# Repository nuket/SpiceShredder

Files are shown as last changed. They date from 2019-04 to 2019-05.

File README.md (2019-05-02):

# IKEA Spice Shredder

This is a project to motorize an [IKEA IHÄRDIG](https://www.ikea.com/ms/en_US/usearch/?query=IH%C3%84RDIG) spice grinder using a 3D-printed drill adapter.

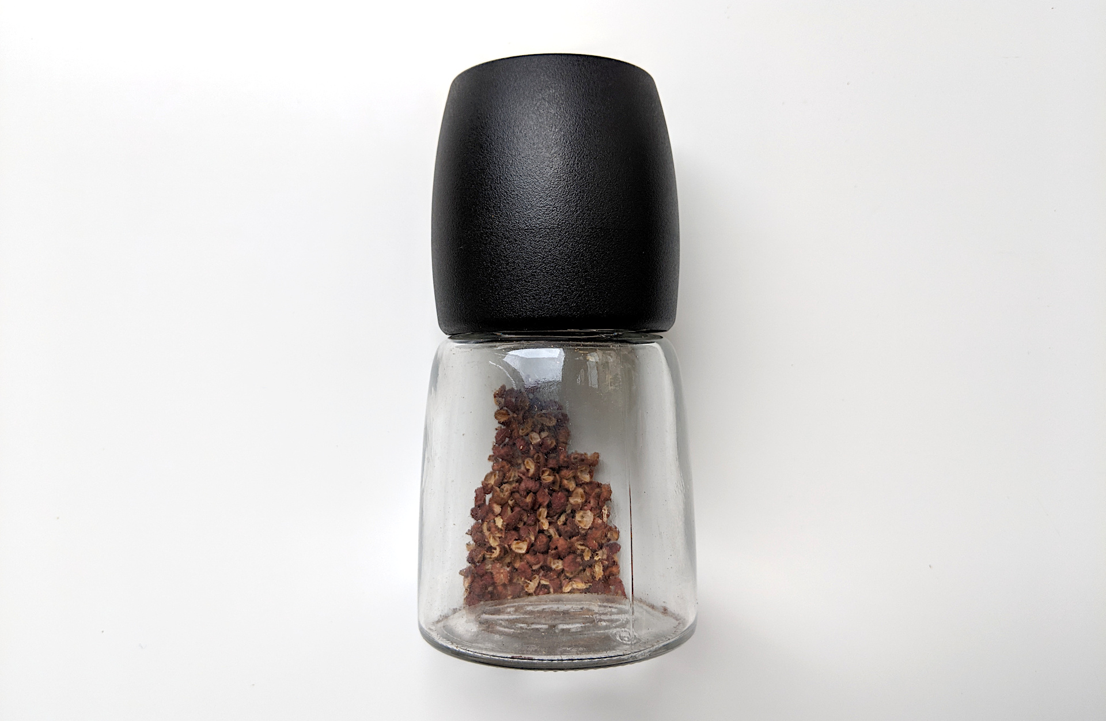
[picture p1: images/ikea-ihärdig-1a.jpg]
IKEA IHÄRDIG spice grinder


Anytime you motorize a grinder, it should be called a shredder.

## Video

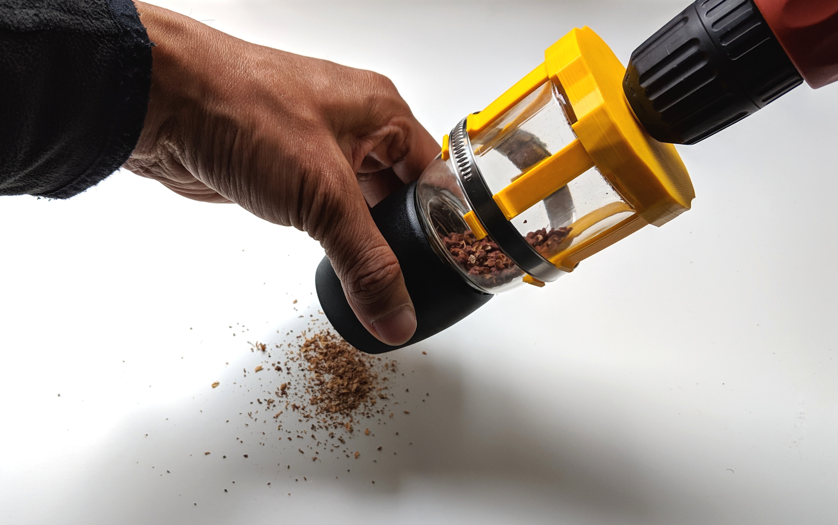
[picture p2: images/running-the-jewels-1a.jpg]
Click to open video of Spice Shredder in action (https://vilimpoc.org/media/running-the-spiceshredder-1920p24-4096k.mp4)


Click to open video of the Spice Shredder in action.

## Rationale

After spending 15 minutes using this spice grinder to make curry powder from whole spices by hand (and nearly getting a repetitive stress injury with the clockwise twisting), I decided that the best solution would be to hook up a drill, and use electricity to do the work instead.

Electric coffee and spice grinders are expensive. IKEA is affordable. And 3D printing is pretty cheap too, once you have a printer.

So the idea is to create an adapter that can grip the spice grinder and rotate it rapidly.

It took three modeling attempts to do so, and since you learn a lot from failure, the whole process is captured here.

## Measurements

The IHÄRDIG spice grinder has a 6.5cm diameter base, and tapers slightly inwards about 1 - 1.5mm at  5 centimeters up the cylinder. I don't have a measurement [caliper](https://en.wikipedia.org/wiki/Calipers), so I had to eyeball these dimensions.

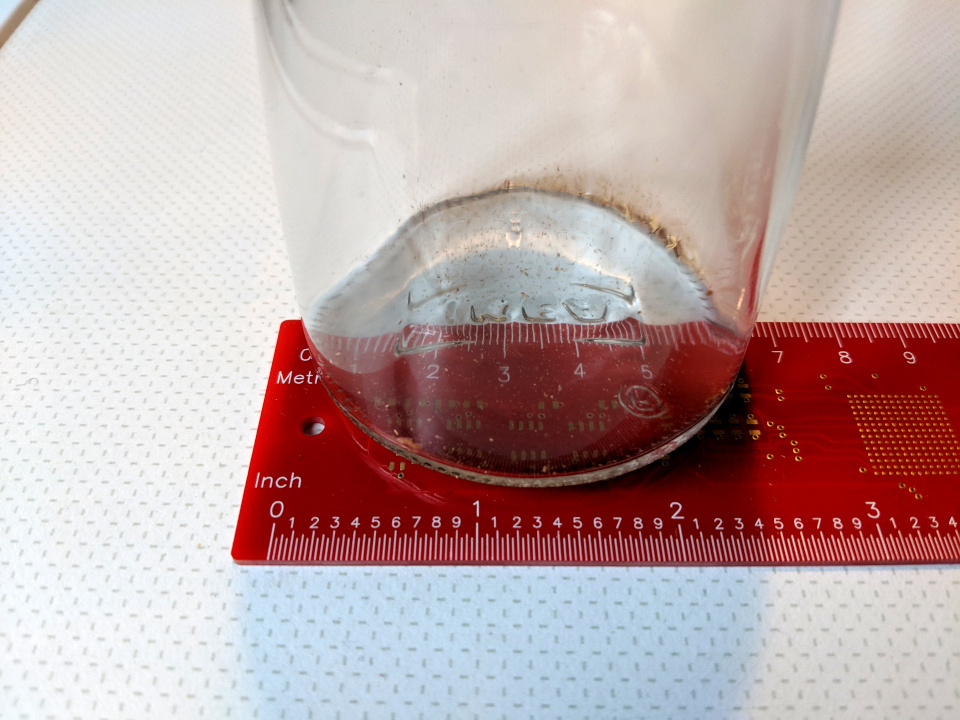
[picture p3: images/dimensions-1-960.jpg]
Spice grinder measurements


The business end of the largest hex-head driver in a standard IKEA [FIXA](https://www.ikea.com/ms/en_US/usearch/?query=fixa) toolkit is around 3 - 3.5mm per edge and 1cm long.

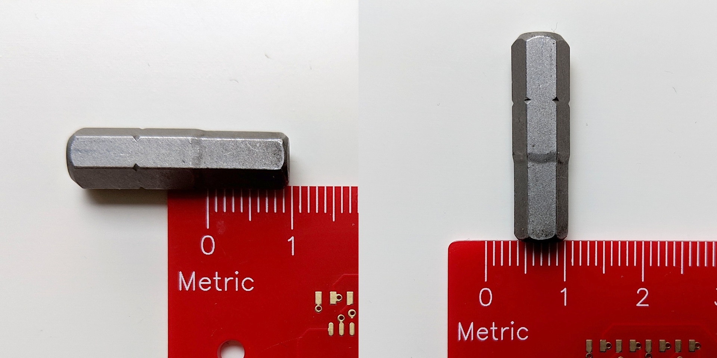
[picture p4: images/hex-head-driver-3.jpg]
IKEA FIXA hex-head driver measurements


## Model 1 (Fail)

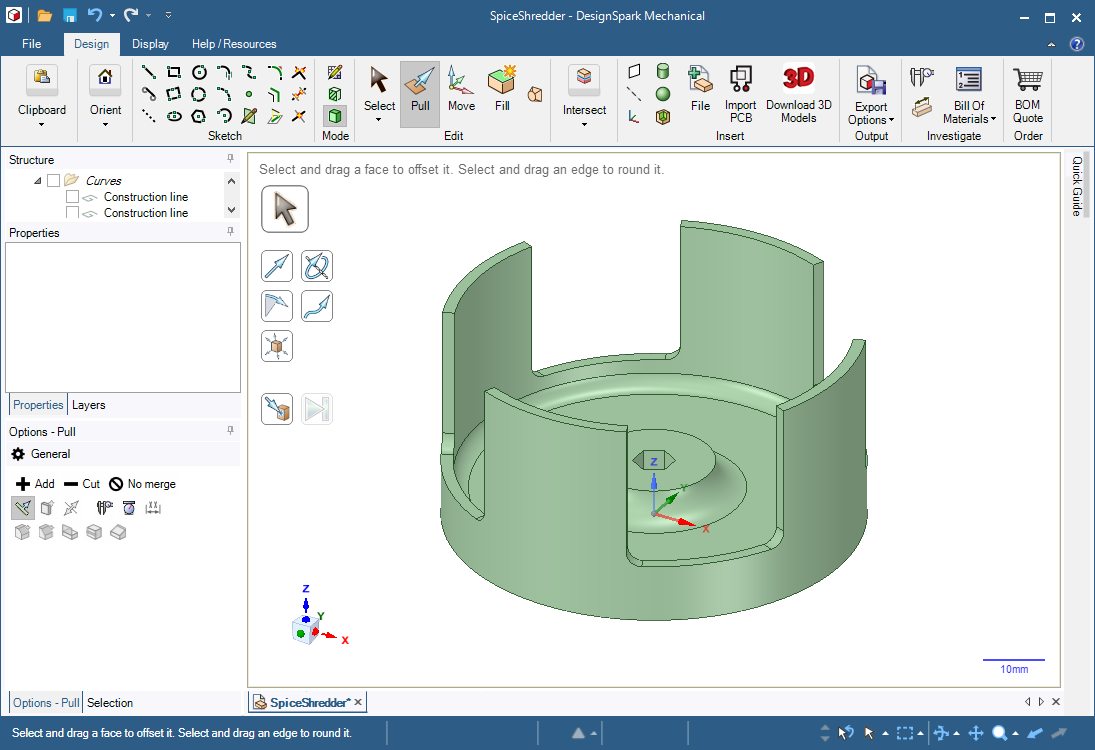
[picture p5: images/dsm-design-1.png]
Model 1 Design in DesignSpark Mechanical


This does not work because the way the walls are printed up, they are brittle and inflexible.

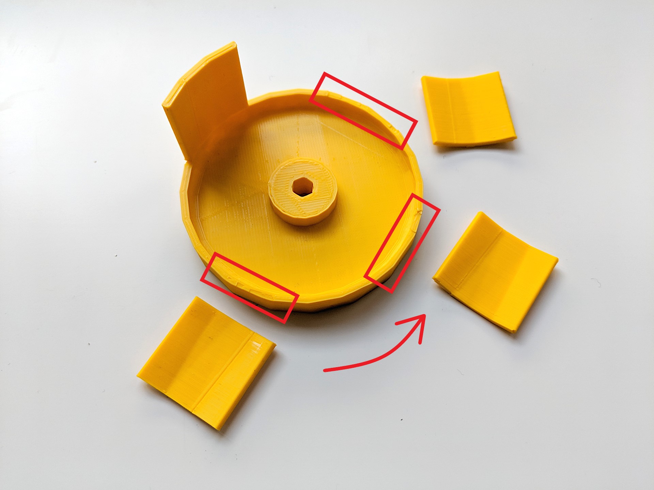
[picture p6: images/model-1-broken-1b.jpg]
Broken tines after printing


The base is printed in concentric circles in the direction of the arrow. The 2mm-thick tines are attached in the same way. They simply _cannot_ flex, so at every connection point to the base, these parts break off instantly.

Also, the hole for the hex-head driver is too small.

## Model 2 (Fail)

This model splits the adapter into two pieces that are assembled: the base and the tines.

This is necessary, because there is no way to mix the direction of printing within a single model — the base and tines use fibers perpendicular to one another.

The base can be printed cleanly from bottom to top with concentric circles and infill, and it can be completely rigid.

The [tines](https://www.dictionary.com/browse/tines) must be printed lengthwise, because we need long polymer fibers that are flexible, unlike the densely-stacked short fibers in Model 1.

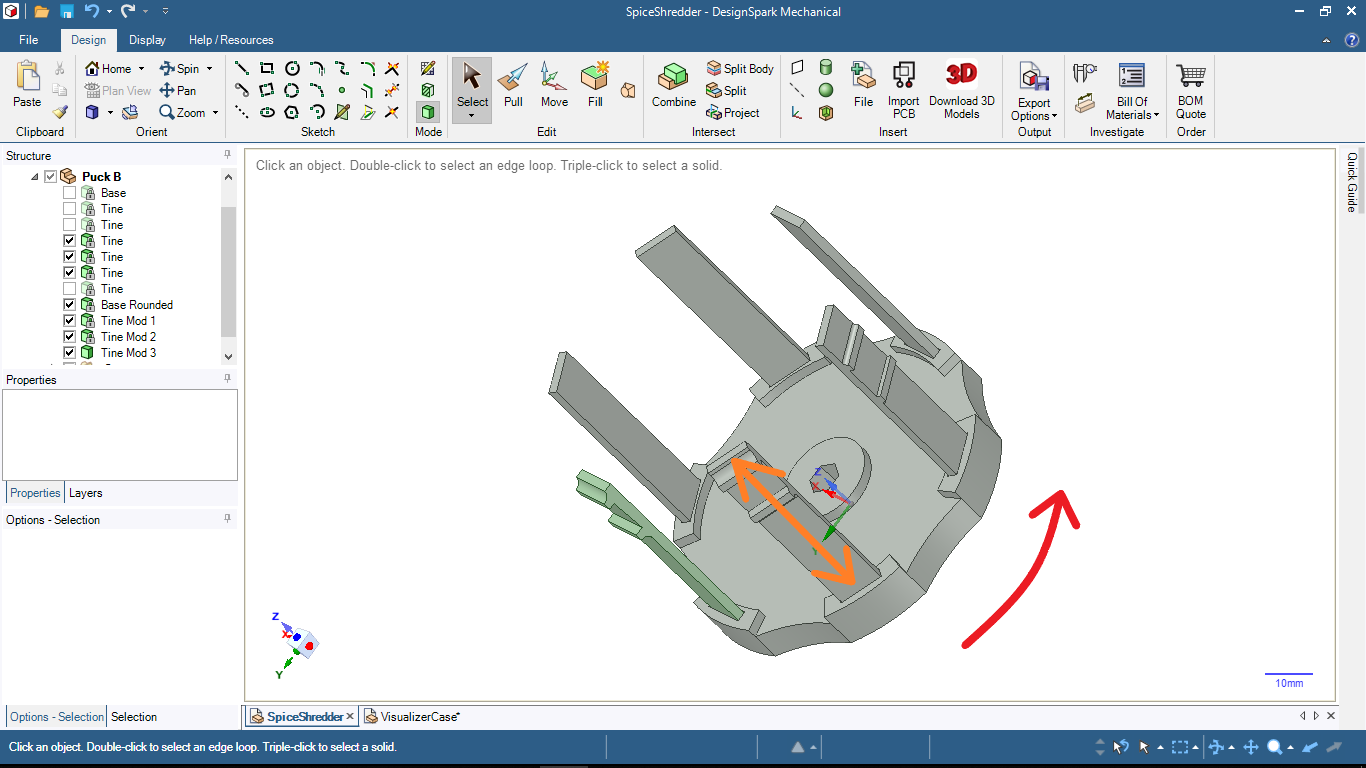
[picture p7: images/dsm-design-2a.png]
Model 2 Design in DesignSpark Mechanical


The picture above shows three slightly different designs for the tines, to be tested out.

This model almost works, the hole for the hex-head driver is perfectly sized. The problem is that the cylinder which grips the hex-head driver is slightly too short. So the driver sticks out by about 0.5mm, and it runs into the bottom of the spice grinder.

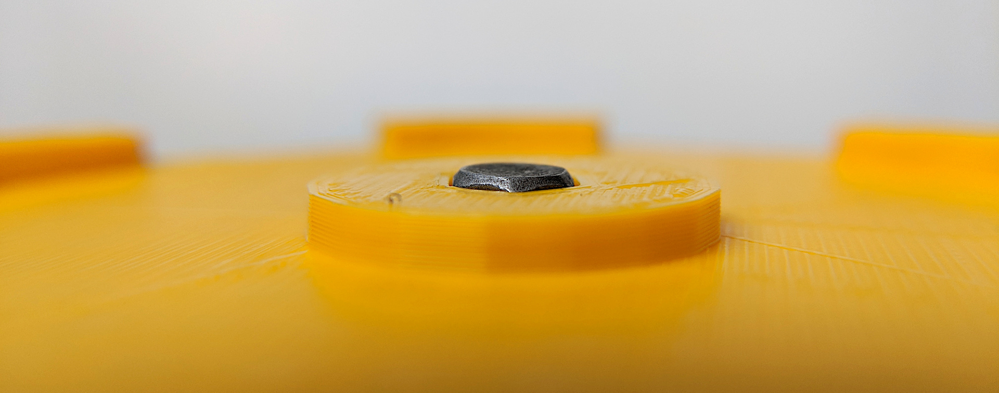
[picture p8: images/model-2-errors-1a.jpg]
Hex-head driver sticks out of cylinder


Also, there's some wasted plastic here.

## Model 3 (Win!)

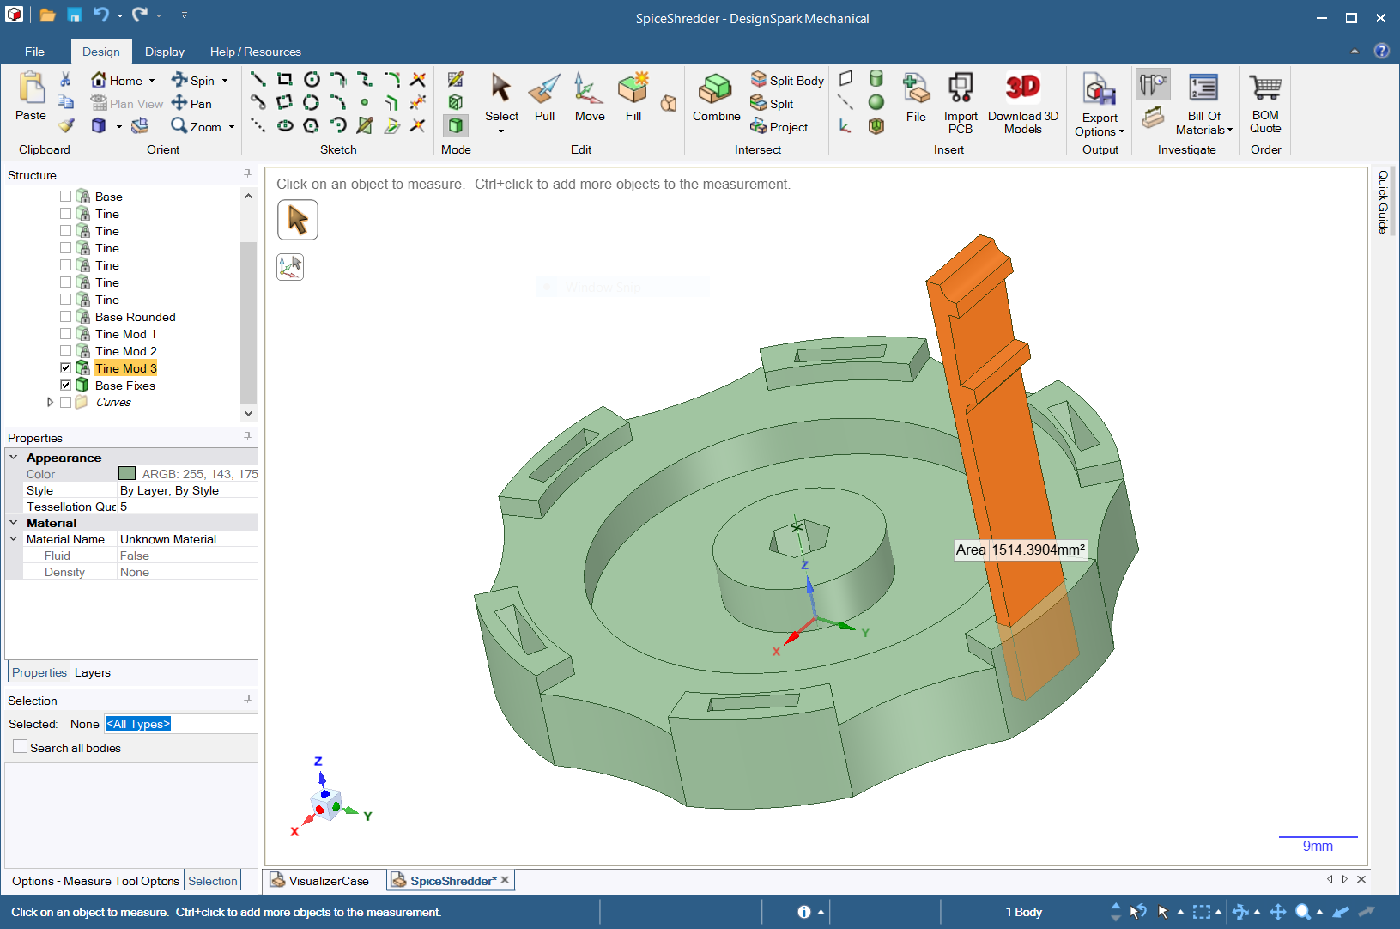
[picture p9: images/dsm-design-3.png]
Model 3 Design in DesignSpark Mechanical


This model corrects all of the issues in the other designs, and removes some unused plastic.

After printing a single test copy of the most-likely best tine model, I went ahead and printed five more like it. Then, I assembled these items together.

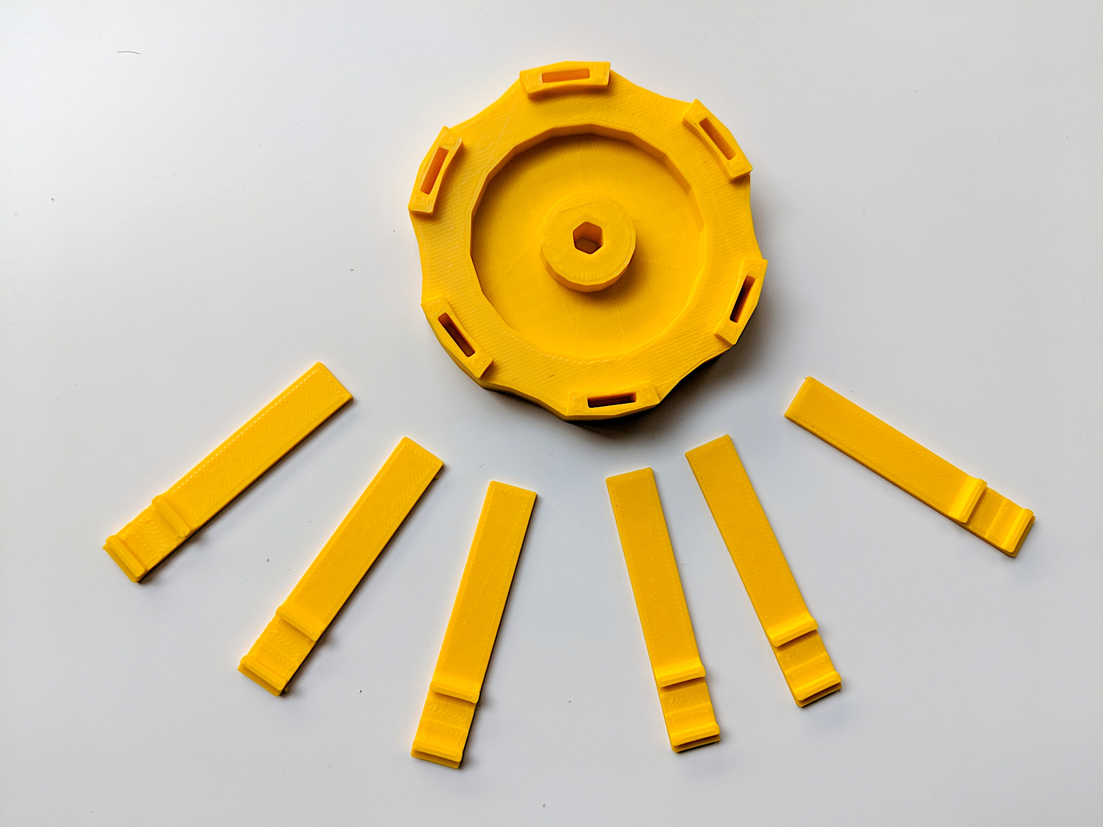
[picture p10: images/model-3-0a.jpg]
Printed Model 3 with base and tines separated


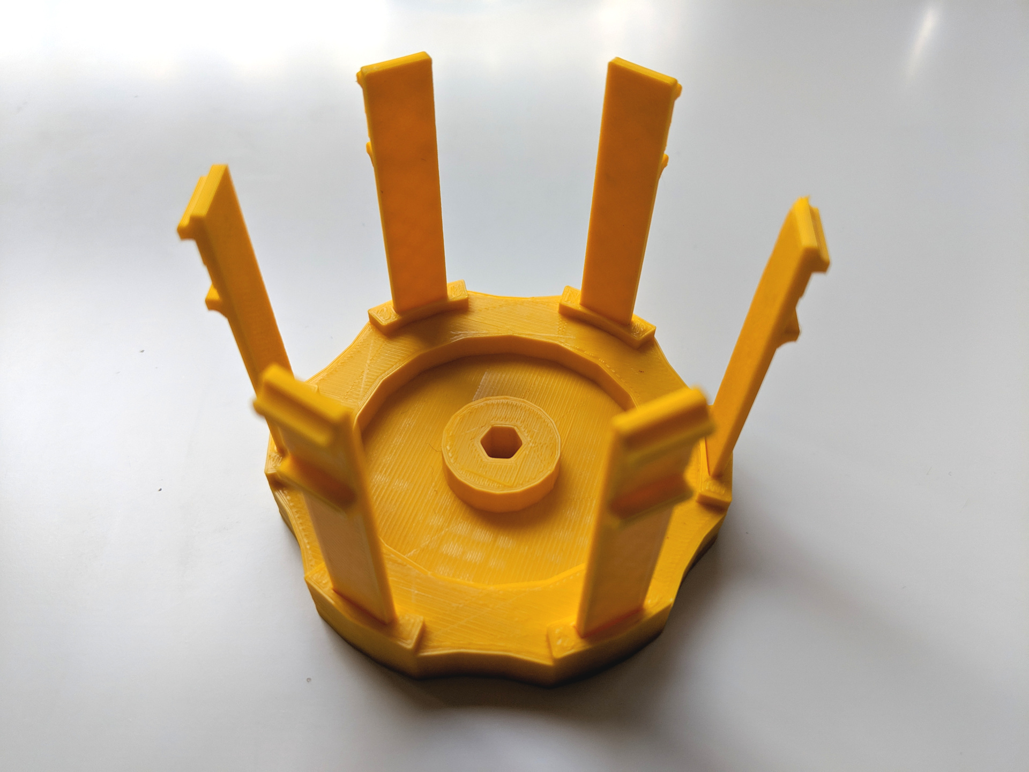
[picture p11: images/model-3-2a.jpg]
Printed Model 3 with tines slotted into the base


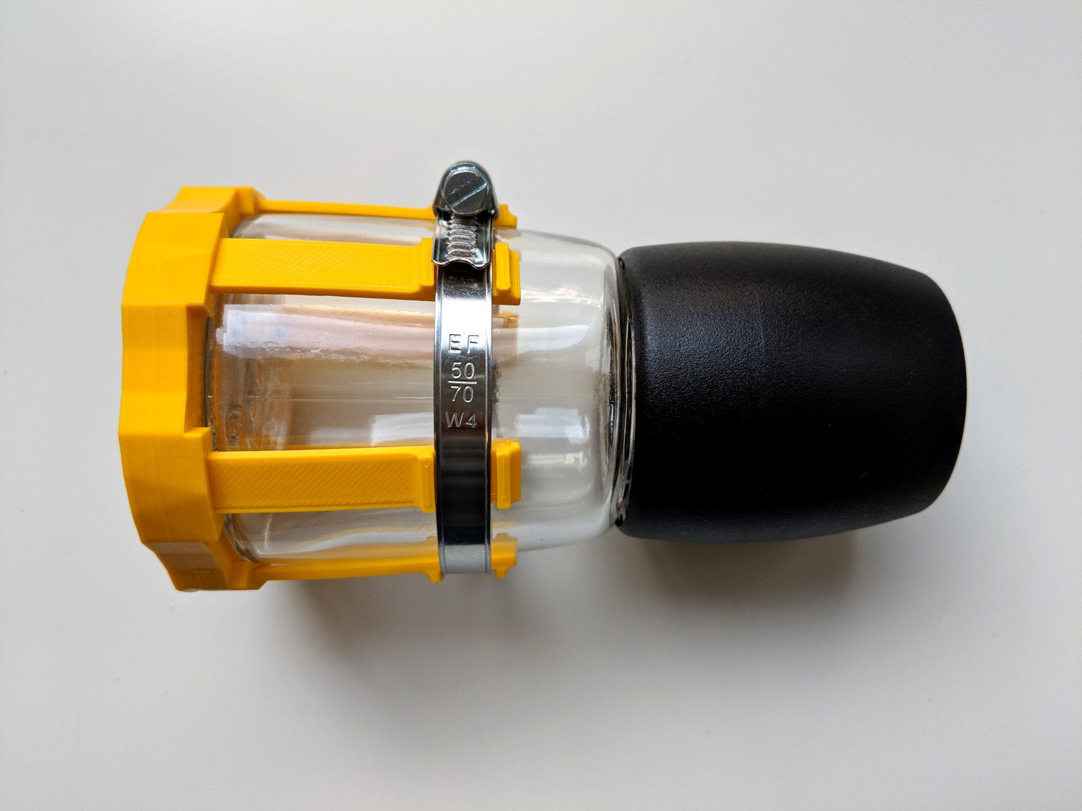
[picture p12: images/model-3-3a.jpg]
Printed Model 3 attached to IHÄRDIG spice grinder with hose clamp


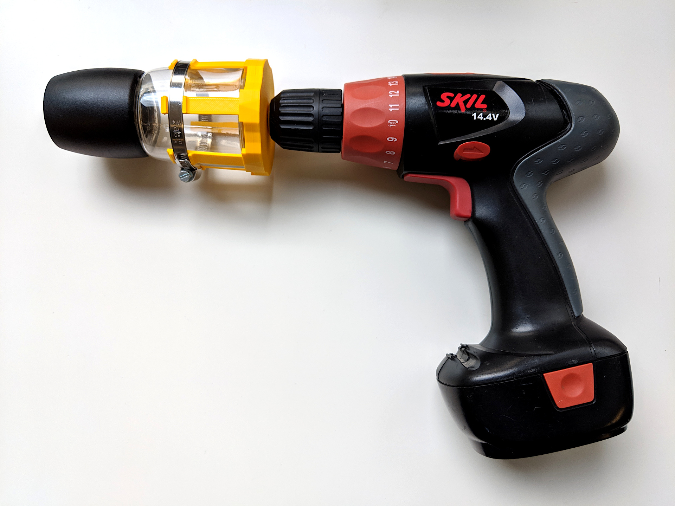
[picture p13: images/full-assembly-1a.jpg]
Full assembly attached to cordless power drill


To make the adapter grip the glass, we tighten an adjustable hose clamp around the tines, pressing them against the glass jar.

There's one other feature to this tine as well. Because the top of the glass jar is narrower than the base, we have to add a small inclined plane, to account for when the hose clamp grips all 6 tines and they all flex inward to grip the glass.

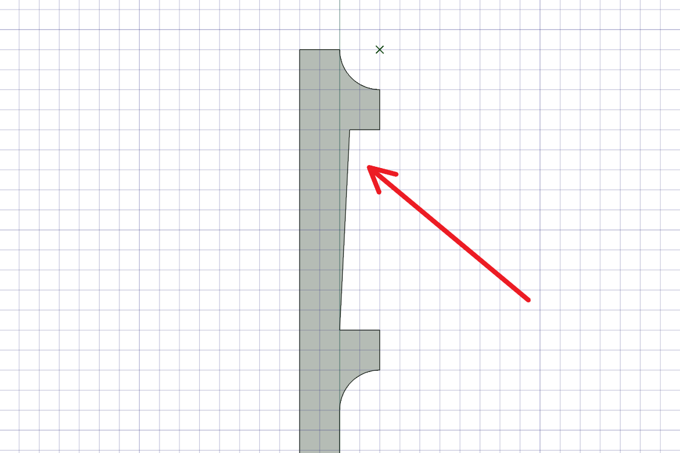
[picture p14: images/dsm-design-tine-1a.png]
Illustration of tine with inclined plane indicated


The hose clamp is standard stainless 9mm width x 50 - 70mm diameter. In Germany, these are easy to source online; in the US, I'm pretty sure any Home Depot would have them.

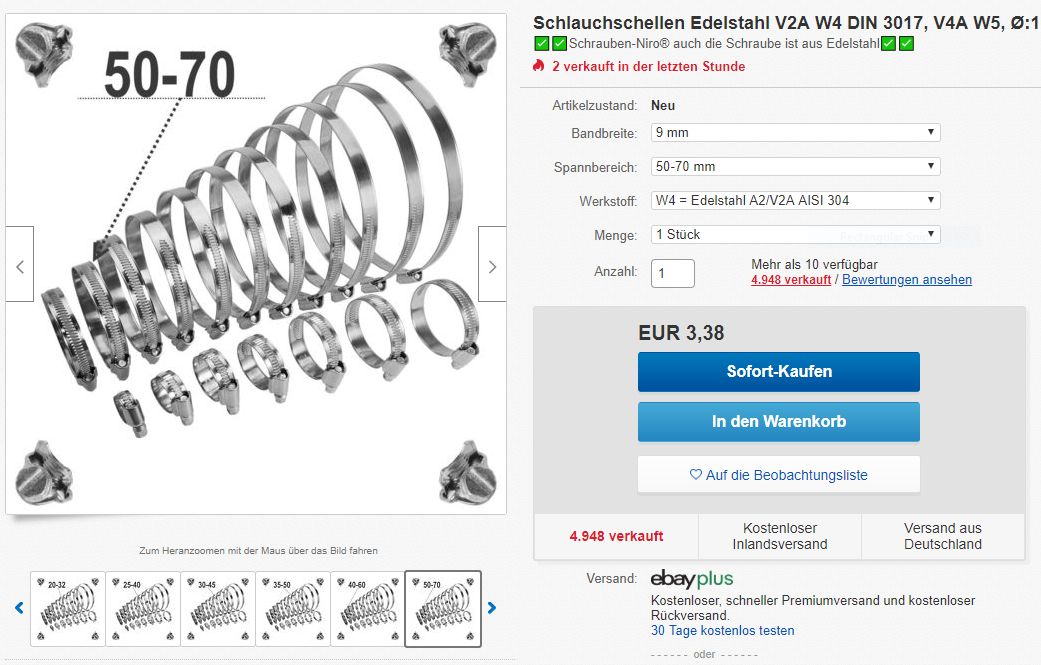
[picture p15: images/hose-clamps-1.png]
Picture of hose clamp auction on eBay Germany


Happy grinding, people! 😉

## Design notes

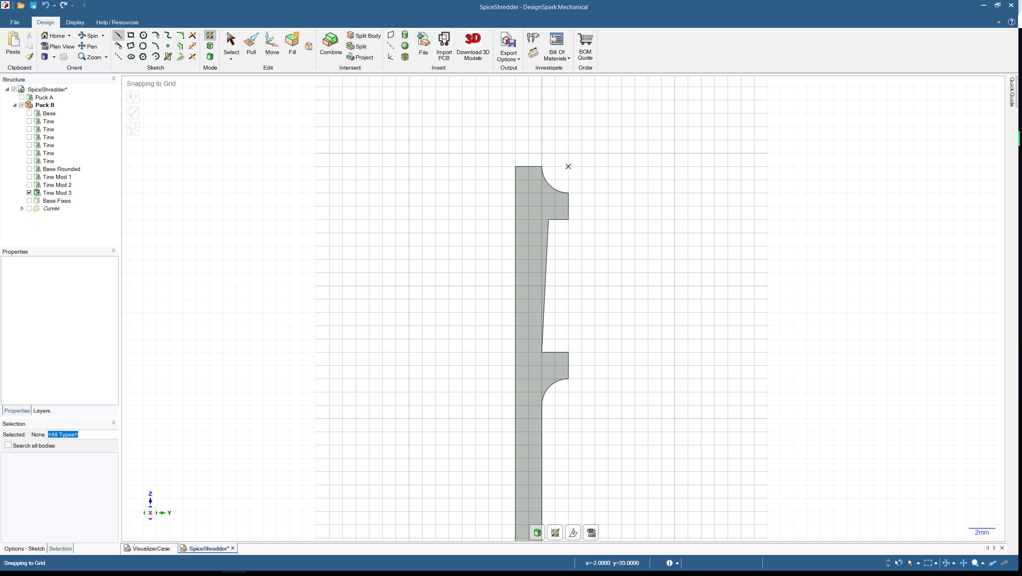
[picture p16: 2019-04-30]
images/dsm-design-tine-1.png

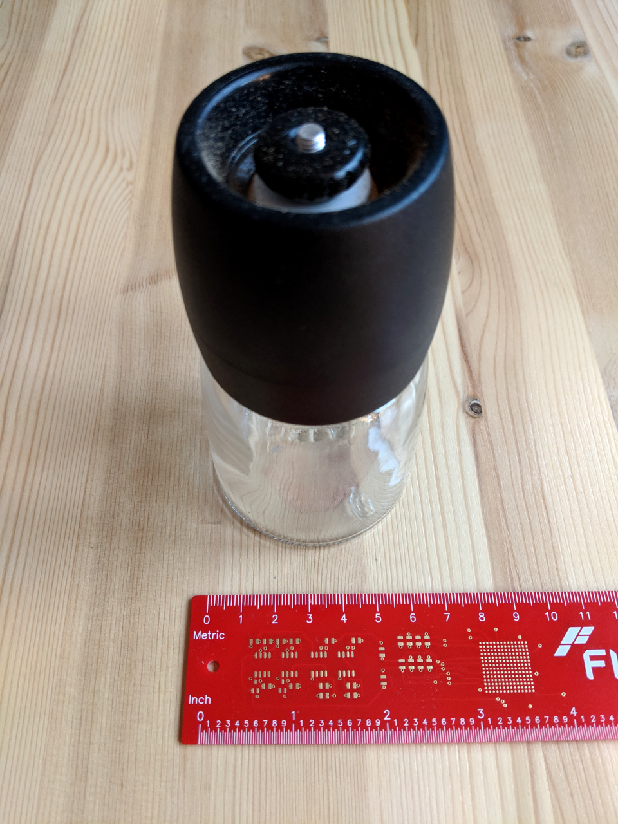
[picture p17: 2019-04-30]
images/dimensions-2-960.jpg

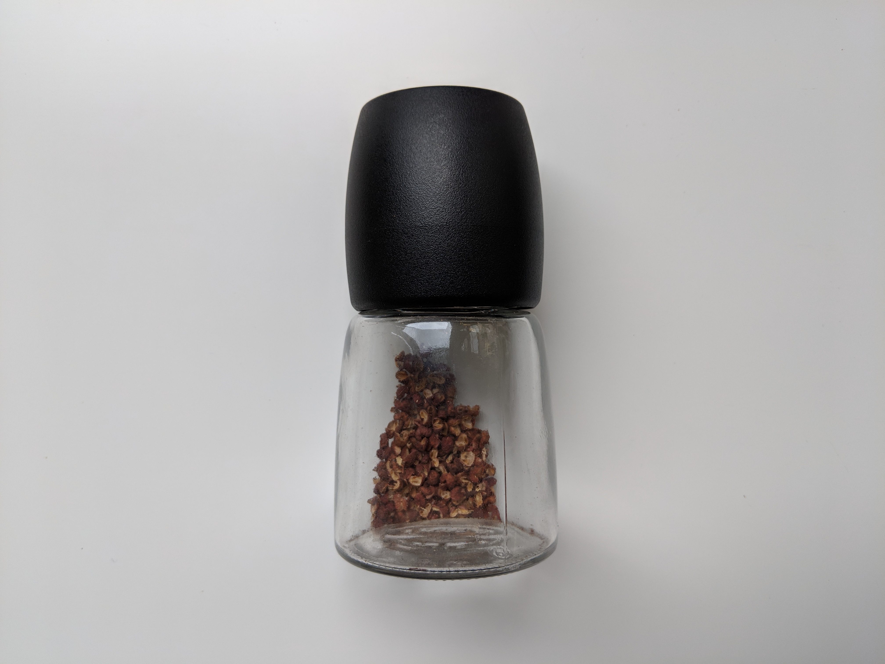
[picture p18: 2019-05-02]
images/ikea-ihärdig-1.jpg

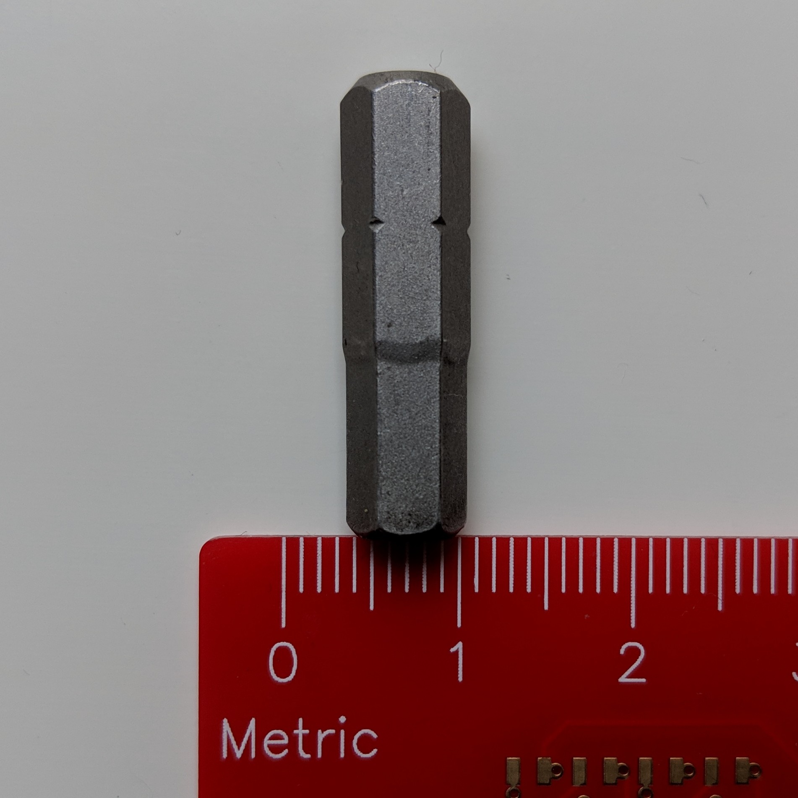
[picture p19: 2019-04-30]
images/hex-head-driver-2.jpg

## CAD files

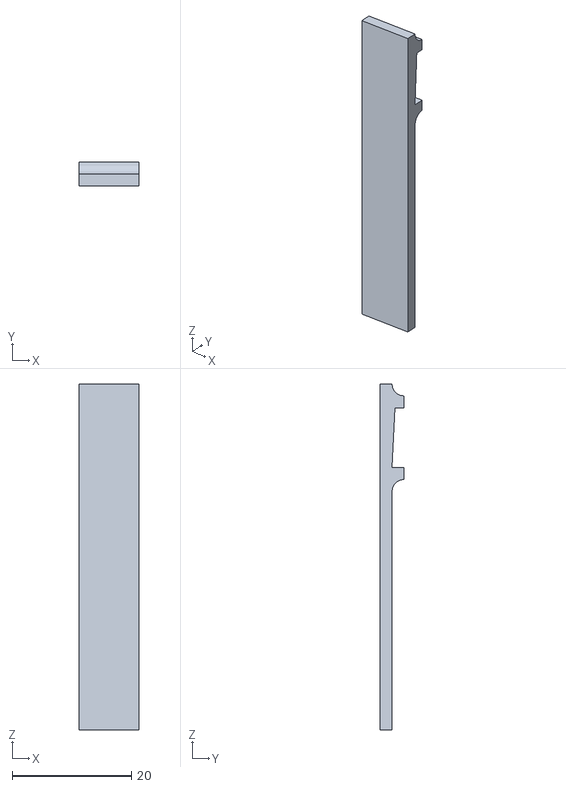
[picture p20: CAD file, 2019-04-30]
SpiceShredderTine.stl
10.0 x 4.00 x 58.0

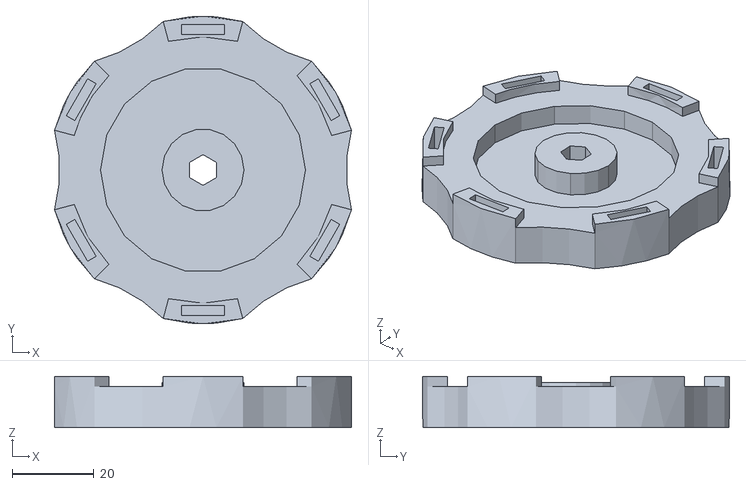
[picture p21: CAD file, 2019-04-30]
SpiceShredderBase.stl
72.4 x 75.0 x 12.5
